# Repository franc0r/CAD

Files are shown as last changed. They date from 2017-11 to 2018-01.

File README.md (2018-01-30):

<h1>FRANCOR - Franconian Open Robotics</h1>
<h2>CAD - Computer Aided Design Data of Robots</h2>

<h3>Overview</h3>
In this repository you can find the CAD data of all concepts and robots build
by the RoboCup Rescue Team FRANCOR.

<h3>Concepts</h3>

<h4>1. Concept: 8-Wheel Robot</h4>

The first meeting result in a concept of a 4 wheel drive robot based on the SummitXL Robot from Robotnik. The idea was to use 8 wheel hub drives to get enough power. This concept was quickly rejected, because it was to difficult to develop a cheap suspension. Furthermore the all-terrain mobility was not too good ( Problems with climbing stairs ).

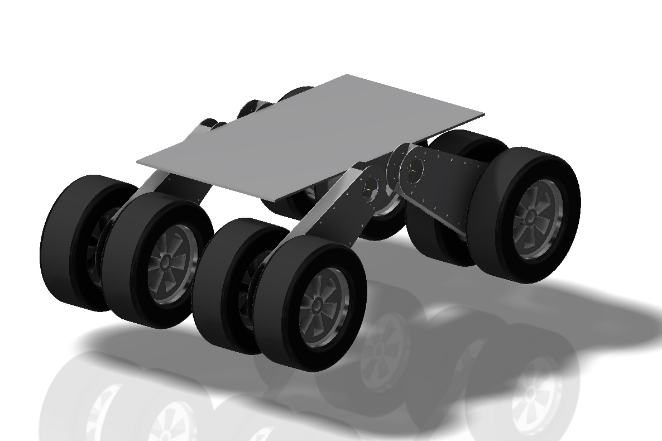
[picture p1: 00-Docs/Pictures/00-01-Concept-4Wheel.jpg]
Concept-8Wheel


<h4>2. Concept: 4-Wheel Robot</h4>

The second concept was a very simple platform with 4 wheels and no suspension. The idea was to first have a platform which can move ( even when the terrain mobility is very limited ) to set up the system and test software ( Sensors, PCs, ... ).

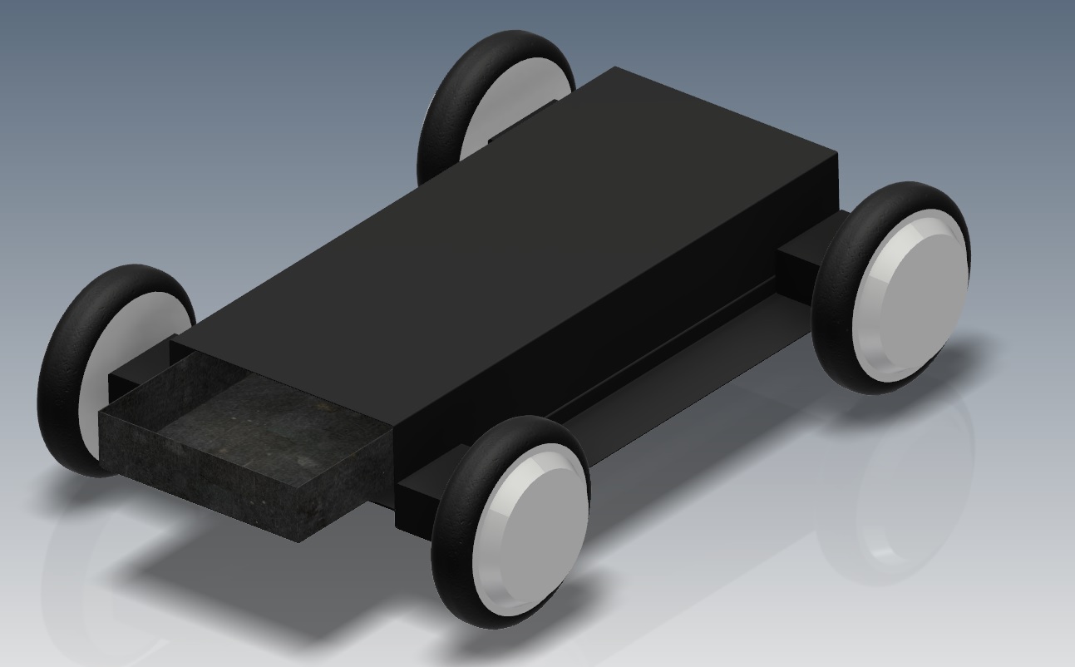
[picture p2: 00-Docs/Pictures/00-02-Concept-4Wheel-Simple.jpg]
Concept-4Wheel


This kind of concept is the first which was build with simple aluminium profiles. But due to the fact, that the terrain mobility is very limited another concept was needed.

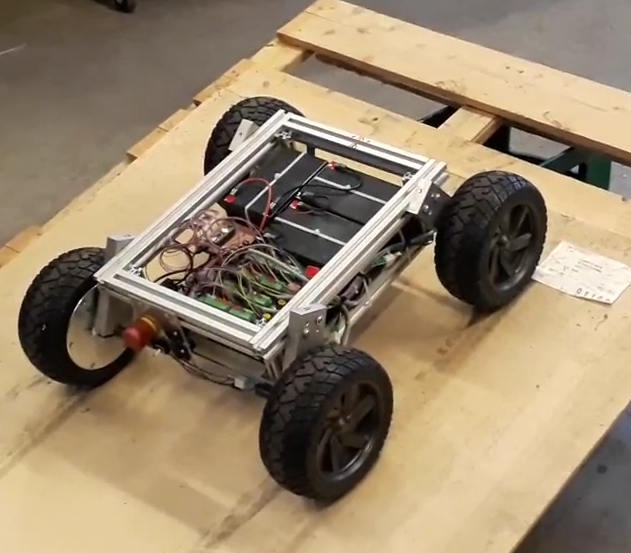
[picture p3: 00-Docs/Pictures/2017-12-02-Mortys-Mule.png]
Mortys-Mule

<br>2017-12-02: Morty's Mule Robot build with aluminium profiles

<h4>3. Concept: Rocker-Bogie Robot</h4>

The next concept is based on the rocker-bogie suspension used for many robots like the NASA Mars Rover Curiosity. The team decided to build a rescue robot based on this concept.
The benefits are a high terrain accesibility and a good compromise of simplicity and costs.

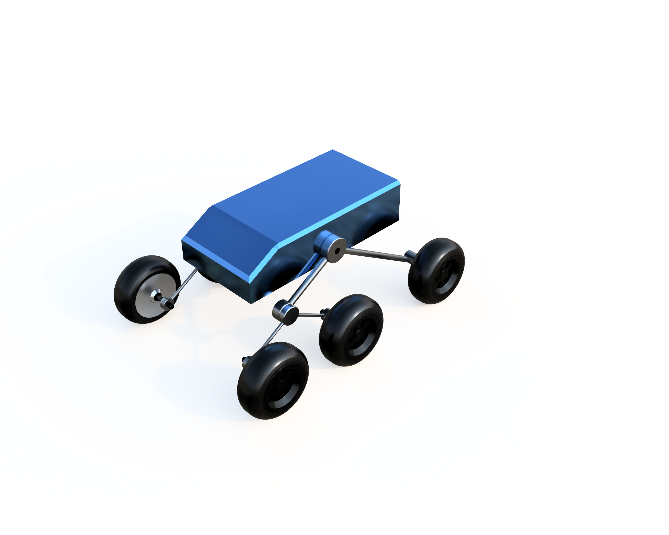
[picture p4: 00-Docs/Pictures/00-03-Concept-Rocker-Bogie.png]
Concept-Rocker-Bogie


This concept is now under heavy development and can hopefully be built at end of the year 2017.

<h3>Current Progress</h3>

It was decided to move the suspension with angled profiles. This concept is now being worked out and the production of the components will start mid/end of December. The schedule provides for the mechanics to be assembled by the end of January.

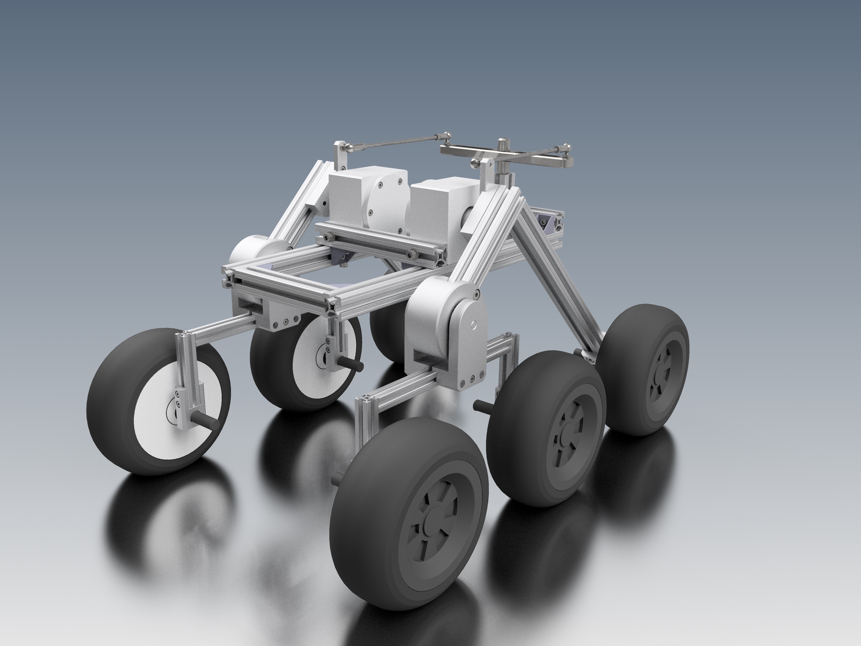
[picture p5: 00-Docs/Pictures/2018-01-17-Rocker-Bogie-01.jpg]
Current-State-2018-01-17

Rocker-Bogie Robot 2018-01-17 with new dimensions and frame.

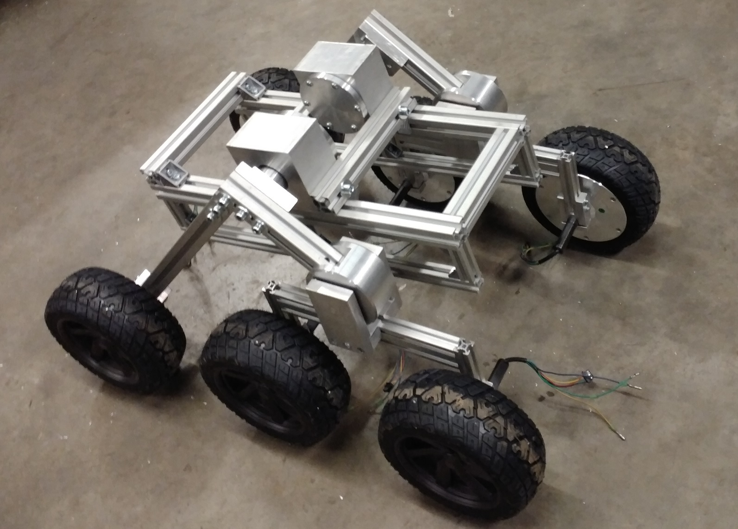
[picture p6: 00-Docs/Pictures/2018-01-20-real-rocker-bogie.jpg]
Real-Rocker-Bogie-Robot

Rocker-Bogie Robot mechanics assembled without differential.

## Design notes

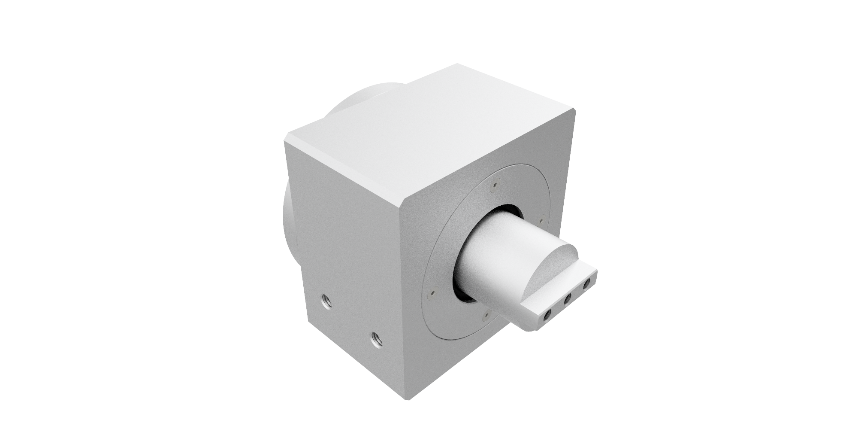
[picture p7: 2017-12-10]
00-Docs/Pictures/2017-12-10-Concept-Rocker-Bogie-02-Rocker-Bearing.png

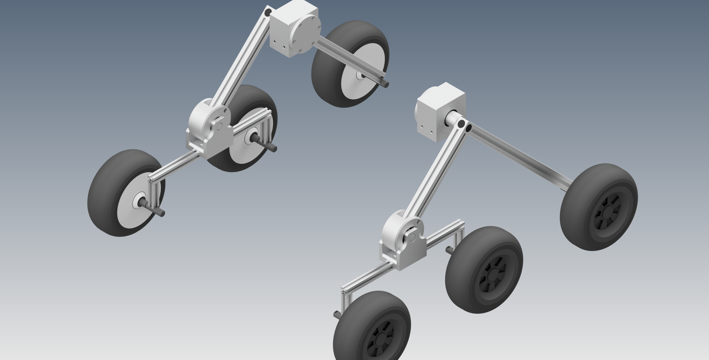
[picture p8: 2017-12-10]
00-Docs/Pictures/2017-12-10-Concept-Rocker-Bogie-01.png

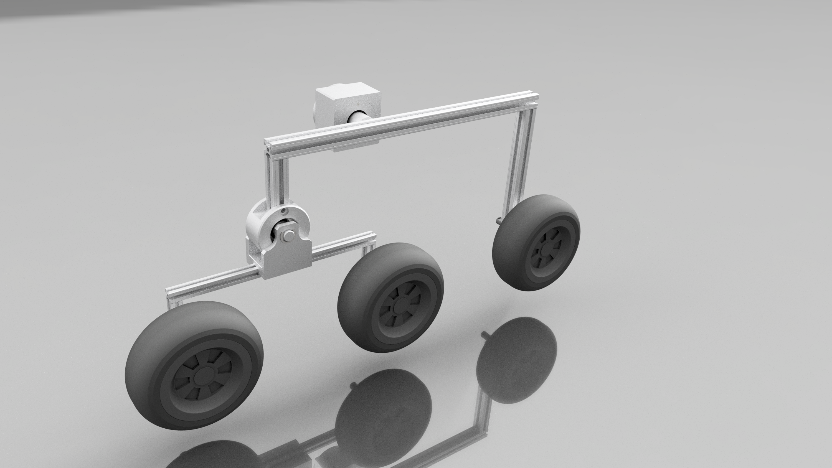
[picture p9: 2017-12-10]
00-Docs/Pictures/2017-12-10-Concept-Rocker-Bogie-02.png

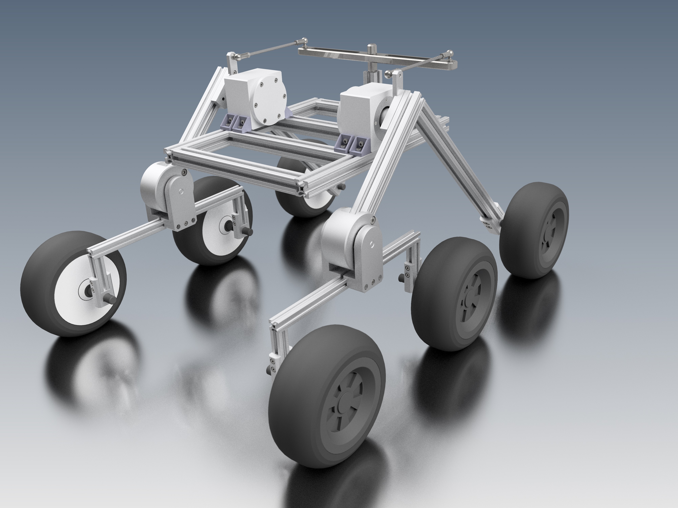
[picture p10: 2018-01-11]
00-Docs/Pictures/2018-01-11-Rocker-Bogie-01.jpg

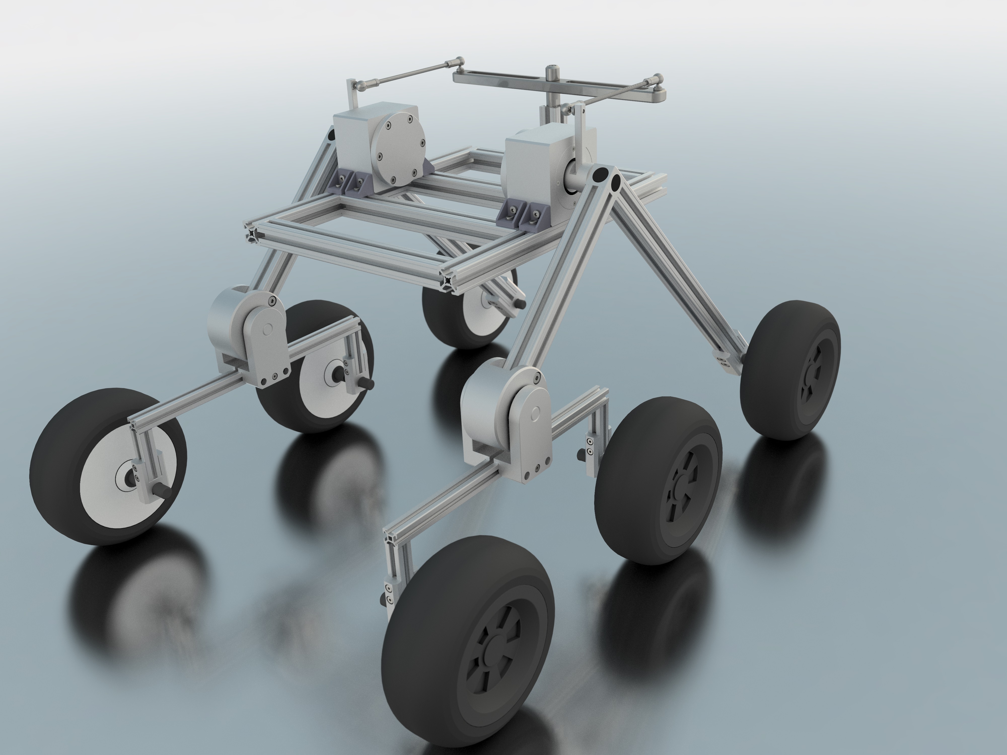
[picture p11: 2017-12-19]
00-Docs/Pictures/2017-12-19-Rocker-Bogie-01.jpg

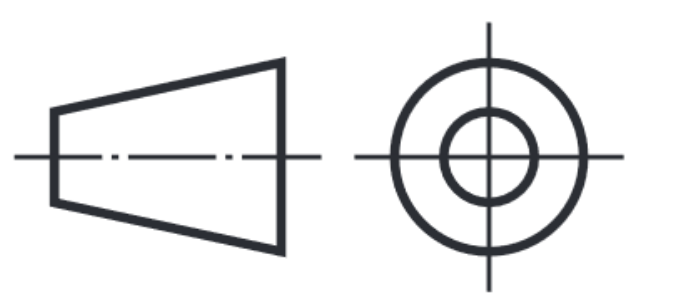
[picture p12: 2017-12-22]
02-Rocker-Bogie-Robot/000-TEMPLATES/projsymb.png

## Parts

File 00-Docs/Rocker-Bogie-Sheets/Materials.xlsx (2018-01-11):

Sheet: Raw-Material
Materials
Part | l [mm] | w [mm] | h [mm] | d [mm] | Cnt | Material
Rocker Housing | 65 | 100 | 100 | - | 2 | Al-6082
Rocker Bearing Housing Cover | 30 | - | - | 105 | 2 | Al-6082
Rocker Profile Connector Rocker Profile Connector Fixation Rocker Bearing Housing Cover Axle | 85/12,5/3,0 | - | - | 40 | 2 | Al-6082
Bogie Bearing Housing and Connector | 50 |  |  | 105 | 2 | Al-6082
Bogie Connector Axle | 85 |  |  | 30 | 2 | Al-6082
Bogie Connector Part 1 | 110 | 60 | 15 | - | 4 | Al-6082
Bogie Connector Part 2 | 29.5 | 60 | 25 | - | 4 | Al-6082
Wheel Connector 20mm Part 1 Wheel Connector 20mm Part 2 | 50/10 | 40 | 20 | - | 4 | Al-6082
Wheel Connector 30mm Part 1 Wheel Connector 30mm Part 2 | 60/10 | 50 | 30 | - | 4 | Al-6082

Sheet: Screws T-Nuts
Screws
Name | Amount | Price | Pkg
Zylinderschraube DIN 7984 M5 x 10 | 20 | 6.45 € | 50
Zylinderschraube DIN 7984 M5 x 12 | 36 | 6.18 € | 50
Zylinderschraube DIN 7984 M6 x 12 | 8 | 5.35 € | 25
Zylinderschraube DIN 7984 M6 x 16 | 8 | 5.39 € | 25
Zylinderschraube DIN 7984 M8 x 12 | 12 | 7.29 € | 25
Senkschraube ISO 10642 M6 x 16 | 2 | 3.37 € | 10
T-Nut
Nutenstein N6 - M5 | 16 | 9.80 € | 20
Nutenstein N8 - M6 | 8 | 9.80 € | 20
Nutenstein N8 - M8 | 12 | 10.00 € | 20

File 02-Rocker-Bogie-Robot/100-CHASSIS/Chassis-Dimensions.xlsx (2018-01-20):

Chassis-Dimensions
Name | Values | Dimensions
Chassis_Frame_Size | 30.00 | mm
Chassis_Length | 500.00 | mm
Chassis_Width | 220.00 | mm
Rocker_Bearing_Size | 100.00 | mm
Rocker_Screw_Distance | 32.50 | mm
Rocker_Screw_Distance_Bottom | 76.00 | mm
Chassis_Bottom_Height | 80.00 | mm

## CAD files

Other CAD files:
02-Rocker-Bogie-Robot/000-TEMPLATES/Standard.dwg
01-Concept/10-SUSP/10-001-ACTR.ipt
01-Concept/10-SUSP/10-001-ACTR_MIR.ipt
01-Concept/10-SUSP/10-001-ACTR_MIR1.ipt
01-Concept/10-SUSP/10-001-ACTR_MIR_MIR.ipt
01-Concept/10-SUSP/10-002-ARM.ipt
01-Concept/10-SUSP/10-003-ARM-CAP.ipt
01-Concept/10-SUSP/10-004-ACTR-FIX.ipt
01-Concept/10-SUSP/10-005-PIPE.ipt
01-Concept/10-SUSP/10-006-ACTR-FIX.ipt
01-Concept/10-SUSP/10-006-ACTR-FIX_MIR.ipt
01-Concept/10-SUSP/10-006-ACTR-FIX_MIR1.ipt
01-Concept/10-SUSP/10-006-ACTR-FIX_MIR_MIR.ipt
01-Concept/10-SUSP/10-SUSP-03.iam
01-Concept/10-SUSP/10-SUSP-03_MIR.iam
01-Concept/10-SUSP/10-SUSP-04_MIR_MIR.iam
01-Concept/10-SUSP/10-SUSP-04_MIR_MIR_MIR.iam
01-Concept/10-SUSP/10-SUSP-ARM-01.iam
01-Concept/10-SUSP/10-SUSP-ARM-02.iam
01-Concept/10-SUSP/10-SUSP-PROFILE-02.iam
01-Concept/10-SUSP/10-SUSP-PROFILE.iam
01-Concept/20-CASE/20-001-CASE.ipt
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

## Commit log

2017-11-18 Added concept to repo
    [10-001-ACTR.ipt, 10-001-ACTR_MIR.ipt, 10-001-ACTR_MIR1.ipt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]
2017-11-18 Added rocker-bogie robot to repo
    [200-10-ROCKER-BEARING-01.ipt, 200-10-ROCKER-BEARING-02.ipt, 200-10-ROCKER-BEARING-03.ipt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]
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2017-11-20 Added sketch of 30x30 bosch aluminium profile
    [90-50-PROFILES-30x30xSketch.ipt]
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2017-11-20 Started bogie bearing development
    [200-30-ROCKER-BOGIE-BEARING-01.ipt]
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2017-12-07 Added quad connector for alu profiles
    [90-50-PROFILES-QUAD-CONN-20x20.ipt]
2017-12-07 Added new part template with project informations in iproperties
    [Template_Norm.ipt]
2017-12-08 Started simplify rocker connector to be usable with quadratic profile connector
    [200-20-ROCKER-CONNECTOR-01.ipt, 200-20-ROCKER-CONNECTOR-ASM-01.iam]
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2017-12-08 Added 30x30 cubic connector
    [90-50-PROFILES-QUAD-CONN-30x30.ipt]
2017-12-08 Modified to 30x30 connector
    [200-20-ROCKER-ASM-01.iam, 200-20-ROCKER-ASM-01.ipn, 200-20-ROCKER-CONNECTOR-01.ipt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]
2017-12-08 Continued development of rocker
    [200-20-ROCKER-ASM-01.iam, 200-20-ROCKER-CONNECTOR-01.ipt, 200-20-ROCKER-CONNECTOR-ASM-01.iam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]
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2017-12-10 Designed Bogie Bearing and Connector
    [200-10-ROCKER-BEARING-01.ipt, 200-10-ROCKER-BEARING-02.ipt, 200-10-ROCKER-BEARING-03.ipt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]
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2017-12-10 Added different profile lenghts
    [90-50-PROFILES-30x30x100.ipt, 90-50-PROFILES-30x30x220.ipt, 90-50-PROFILES-30x30x275.ipt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]
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2017-12-14 Replaced old bogie connector with new one build out of plates and two distance blocks
    [200-20-ROCKER-ASM-01.iam, 200-20-ROCKER-CONNECTOR-ASM-01.iam, 200-30-BOGIE-BEARING-ASM-01.iam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]
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2017-12-16 Added angle connectors to rocker bearing and replaced ISO 4762 screws with DIN 7984 ( small head )
    [200-10-ROCKER-BEARING-01.ipt, 200-10-ROCKER-BEARING-02.ipt, 200-10-ROCKER-BEARING-ASM-01.iam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]
2017-12-16 Added N6 M5 profile connector
    [900-50-PROFILES-CONN-N6xM5.ipt]
2017-12-16 Added fix elements
    [200-30-BOGIE-BEARING-ASM-01.iam, 200-30-ROCKER-BOGIE-BEARING-01.ipt, 200-40-BOGIE-CONNECTOR-03.ipt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]
2017-12-16 Created asm for complete robot and frame
    [100-CHASSIS-ASM-01.iam, 200-10-CHASSIS-FRAME-ASM-01.iam, 90-50-PROFILES-30x30x350.ipt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]
2017-12-16 Added middle profiles to frame
    [100-CHASSIS-ASM-01.iam, 200-10-CHASSIS-FRAME-ASM-01.iam, Rocker-Bogie-Robot-ASM-01.iam]
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2017-12-17 Updated folder groups of project
    [200-10-ROCKER-BEARING-01.ipt, 200-10-ROCKER-BEARING-02.ipt, 200-10-ROCKER-BEARING-03.ipt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]
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2017-12-18 Added DIN7984 M5x10 screw
    [900-40-SCREWS-DIN7984_M5x10.ipt]
2017-12-18 Renamed wheel connector and completed ASM
    [200-50-WHEEL-CONNECTOR-01.ipt, 200-50-WHEEL-CONNECTOR-20MM-01.ipt, 200-50-WHEEL-CONNECTOR-20MM-02.ipt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]
2017-12-18 Created 30mm wheel connector
    [200-50-WHEEL-CONNECTOR-30MM-01.ipt, 200-50-WHEEL-CONNECTOR-30MM-02.ipt, 200-50-WHEEL-CONNECTOR-30MM-ASM-01.iam]
2017-12-18 Updated distance of connector in ASM
    [200-50-WHEEL-CONNECTOR-20MM-ASM-01.iam]
2017-12-18 Updated ASM to current state
    [200-ROCKER-BOGIE-ASM.iam, Rocker-Bogie-Robot-ASM-01.iam]
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2017-12-18 Started developing differential Updated main ASM to contain both sides
    [200-10-ROCKER-BEARING-ASM-01.iam, 200-10-ROCKER-BEARING-PROFILE-CONN-ASM-02.iam, 200-20-ROCKER-CONNECTOR-01.ipt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]
2017-12-18 Small fix
    [200-20-ROCKER-CONNECTOR-ASM-02.iam, 200-60-DIFFERENTIAL-BAR-02.iam, 200-ROCKER-ASM-02.iam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]
2017-12-18 Continued development of differential
    [200-20-ROCKER-CONNECTOR-ASM-01.iam, 200-20-ROCKER-CONNECTOR-ASM-02.iam, 200-60-DIFFERENTIAL-BAR-01.iam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]
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2017-12-19 Changed assemblys to allow dynamic tests
    [200-01-ROCKER-BEARING-ASM.iam, 200-02-ROCKER-CONNECTOR-ASM-L.iam, 200-02-ROCKER-CONNECTOR-ASM-R.iam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]
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2017-12-23 Adjustments of rocker bearing housing
    [200-02-ROCKER-CONNECTOR-ASM-L.iam, 200-02-ROCKER-CONNECTOR-ASM-R.iam, 200-03-BOGIE-CONNECTOR-ASM.iam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]
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2017-12-23 Updated ASM (property update)
    [200-10-ROCKER-BEARING-03.ipt, 200-10-ROCKER-BEARING-ASM-01.iam, 200-10-ROCKER-BEARING-PROFILE-CONN-ASM-01.iam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]
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2017-12-27 Updated parts ( small changes )
    [200-10-ROCKER-BEARING-01.ipt, 200-10-ROCKER-BEARING-03.ipt, 200-10-ROCKER-BEARING-ASM-01.iam]
2017-12-27 Updated drawings for rocker bearing housing
    [00-RAW-DIMENSIONS.dwg, 200-10-ROCKER-BEARING.dwg]
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2017-12-28 Updates description head of drawings with new template
    [200-10-ROCKER-BEARING.dwg]
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2017-12-28 Renamed drawing ( removed .iam in name )
    [200-40-BOGIE-CONNECTOR-01.dwg, 200-40-BOGIE-CONNECTOR-01.iam.dwg]
2017-12-29 Replaced qube connector
    [200-20-ROCKER-CONNECTOR-01.ipt, 200-20-ROCKER-CONNECTOR-03.ipt]
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2017-12-29 Updated assemblies with new rocker connector ( no cube connector )
    [200-02-ROCKER-CONNECTOR-ASM-L.iam, 200-02-ROCKER-CONNECTOR-ASM-R.iam, 200-03-BOGIE-CONNECTOR-ASM.iam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]
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2018-01-04 Changed outer diameter of bogie bearing housing from 64,5 to 62,0
    [200-02-ROCKER-CONNECTOR-ASM-L.iam, 200-02-ROCKER-CONNECTOR-ASM-R.iam, 200-10-ROCKER-BEARING-01.ipt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]
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2018-01-11 Replaced old differential bar with new one which is connected to the rocker connector plate
    [200-20-ROCKER-CONNECTOR-01.ipt, 200-20-ROCKER-CONNECTOR-04.ipt, 200-20-ROCKER-CONNECTOR-ASM-01.iam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]
2018-01-11 Adjusted differential connector to new differential asm. Updated ASMs.
    [200-02-ROCKER-CONNECTOR-ASM-L.iam, 200-02-ROCKER-CONNECTOR-ASM-R.iam, 200-20-ROCKER-CONNECTOR-ASM-01.iam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]
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2018-01-13 Changed fixation of rocker bearing
    [200-10-ROCKER-BEARING-01.ipt, 200-10-ROCKER-BEARING-02.ipt, 200-10-ROCKER-BEARING-03.ipt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]
2018-01-13 Updated rocker connector to new thickness of 20mm instead 15 mm
    [200-02-ROCKER-CONNECTOR-ASM-L.iam, 200-02-ROCKER-CONNECTOR-ASM-R.iam, 200-20-ROCKER-CONNECTOR-01.ipt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]
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2018-01-20 Added 20 x 20 profile angles / updated 30 x 30
    [900-40-SCREWS-DIN7984_M4x8.ipt, 900-50-PROFILES-ANGLE-CONN-20x20-01.iam, 900-50-PROFILES-ANGLE-CONN-20x20.ipt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]
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2018-01-20 Fixed angle profile connector
    [100-10-FRAME-CHASSIS-ASM-01.iam, 100-10-FRAME-PROFILE-LENGTH-01.ipt, 100-10-FRAME-PROFILE-ROCKER-CONNECTOR.ipt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]
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2018-01-20 Changed 20x20 angle connector position at bottom frame
    [100-10-FRAME-CHASSIS-ASM-01.iam, 100-CHASSIS-ASM-01.iam, Rocker-Bogie-Robot-ASM-01.iam]
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2018-01-30 Increasesd bogie connector stability
    [200-03-BOGIE-CONNECTOR-ASM.iam, 200-40-BOGIE-CONNECTOR-ASM-01.iam, 200-40-BOGIE-CONNECTOR-P-01.ipt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]
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
